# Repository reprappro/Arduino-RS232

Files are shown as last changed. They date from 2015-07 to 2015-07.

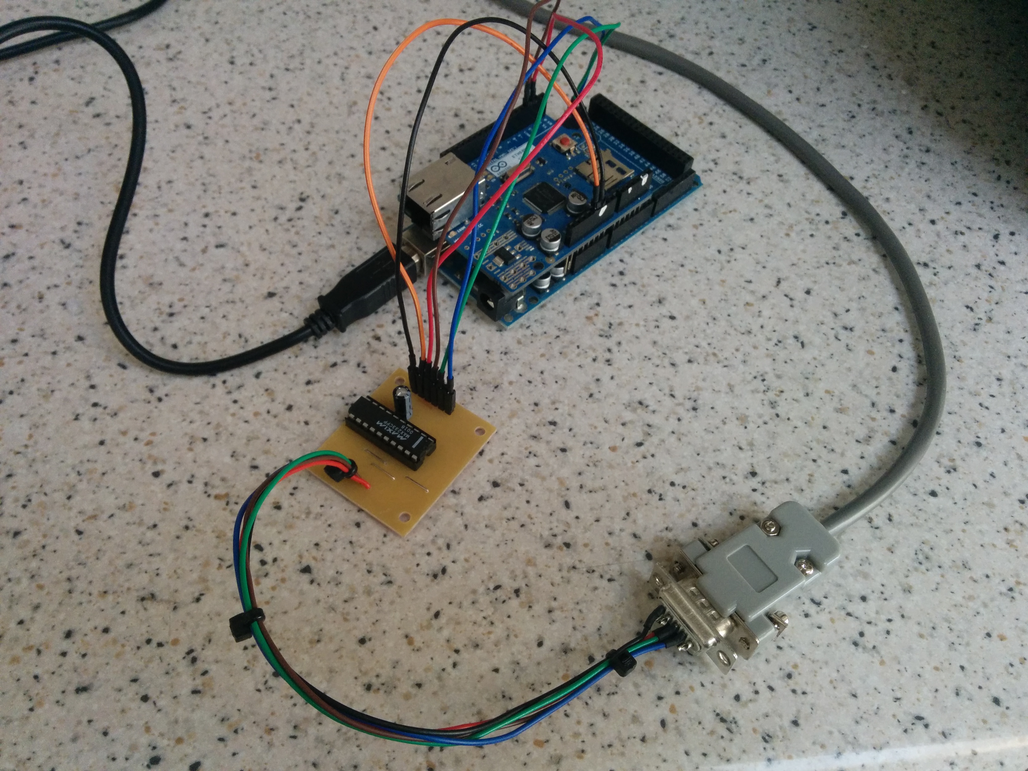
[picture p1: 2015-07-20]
Images/2015-07-17 16.40.09.jpg

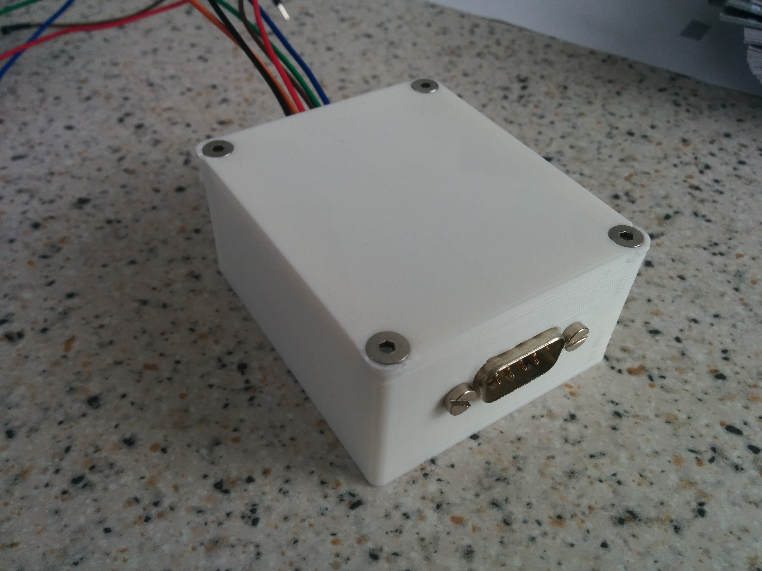
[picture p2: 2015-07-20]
Images/2015-07-20 14.40.57.jpg

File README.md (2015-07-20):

# Arduino-RS232
An RS232 interface circuit for Arduinos.  

It is general-purpose, but it is primarily intended to allow an Arduino to control
a Roland Modela CNC mill (http://www.rolanddg.com/product/3d/3d/mdx-20_15/spec.html).

This allows the Modela to mill PCBs under the control of the Arduino, including the PCB
for the interface circuit itself.  So you breadboard it and get it working.  Then you mill
its PCB.  Then you take the components off your breadboard and solder them onto the PCB...

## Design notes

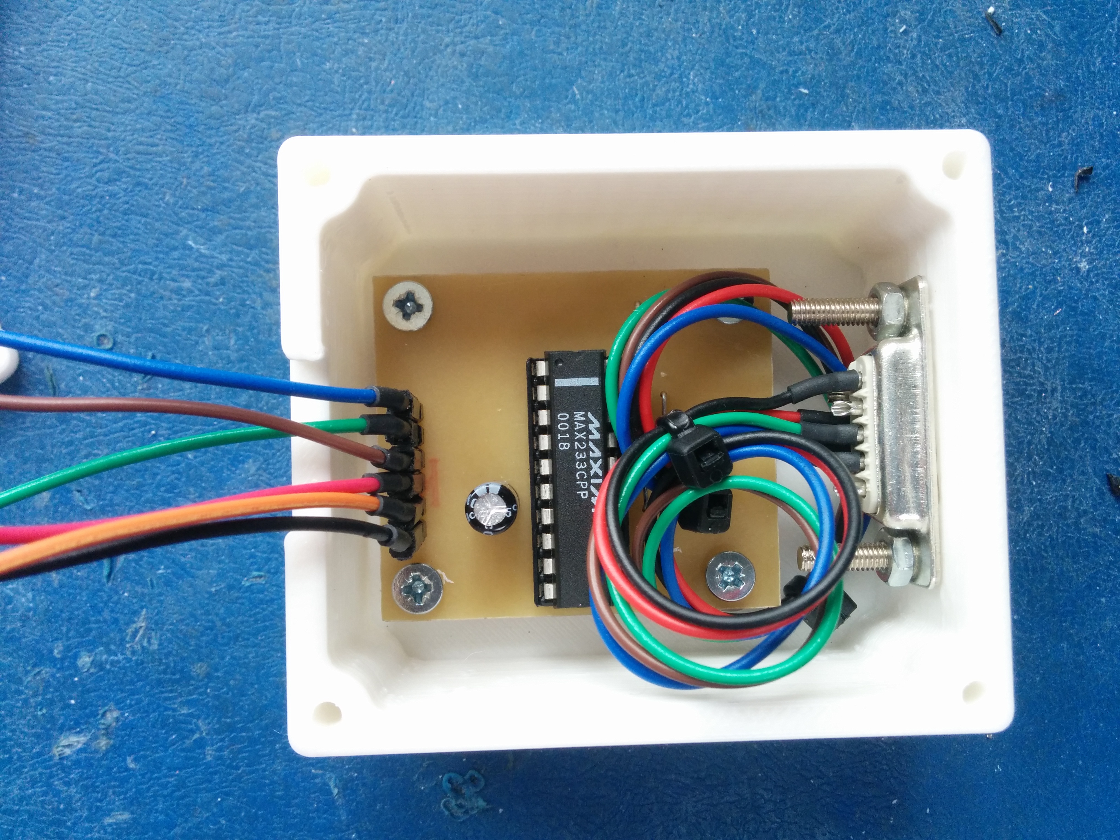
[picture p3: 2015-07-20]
Images/2015-07-20 13.38.10.jpg

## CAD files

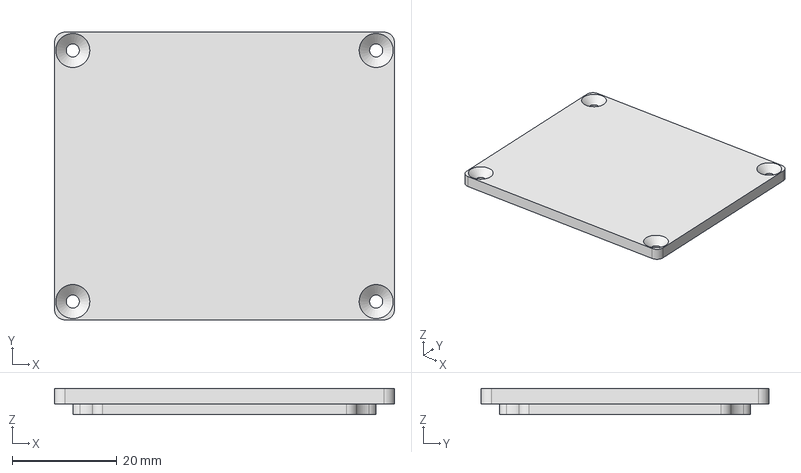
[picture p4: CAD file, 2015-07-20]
Case/Lid.stp
65.0 x 55.0 x 5.00 mm

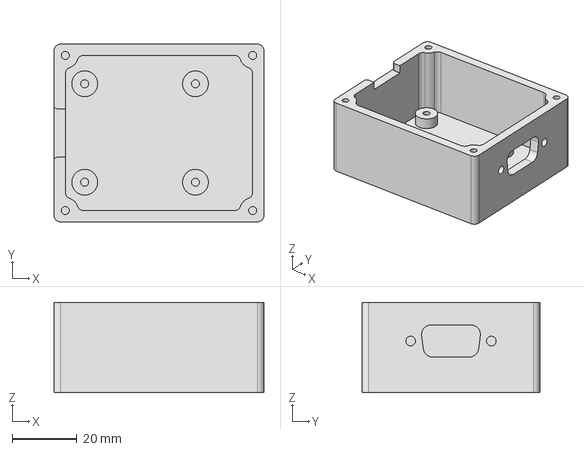
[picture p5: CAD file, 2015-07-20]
Case/Case.stp
65.0 x 55.0 x 28.0 mm

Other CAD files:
Case/Case.stl
Case/Lid.stl

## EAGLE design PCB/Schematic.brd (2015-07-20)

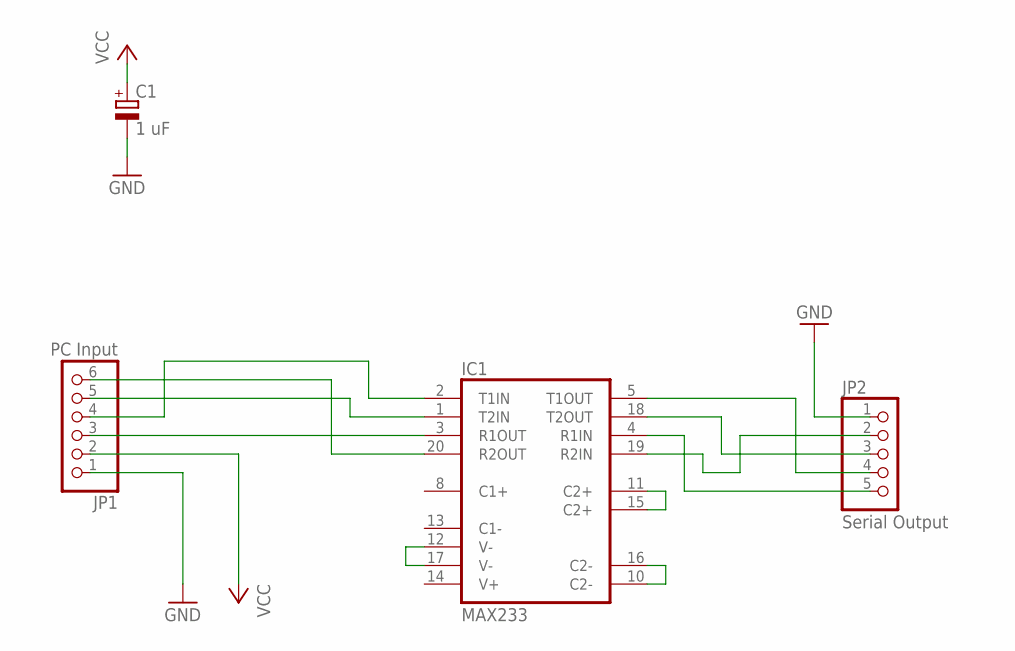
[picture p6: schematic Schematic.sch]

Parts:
C1: 1 uF; E2,5-6
IC1: MAX233; DIL20
JP1: PC Input; 1X06
JP2: Serial Output; 1X05

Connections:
GND: C1.-, IC1.6 (GND), IC1.9 (GND), JP1.1, JP2.1
unnamed: IC1.12 (V-), IC1.17 (V-)
unnamed: IC1.11 (C2+), IC1.15 (C2+)
unnamed: IC1.10 (C2-), IC1.16 (C2-)
unnamed: IC1.20 (R2OUT), JP1.6
unnamed: IC1.1 (T2IN), JP1.5
unnamed: IC1.2 (T1IN), JP1.4
unnamed: IC1.3 (R1OUT), JP1.3
unnamed: IC1.18 (T2OUT), JP2.3
unnamed: IC1.19 (R2IN), JP2.2
unnamed: IC1.5 (T1OUT), JP2.4
unnamed: IC1.4 (R1IN), JP2.5
VCC: C1.+, IC1.7 (VCC), JP1.2

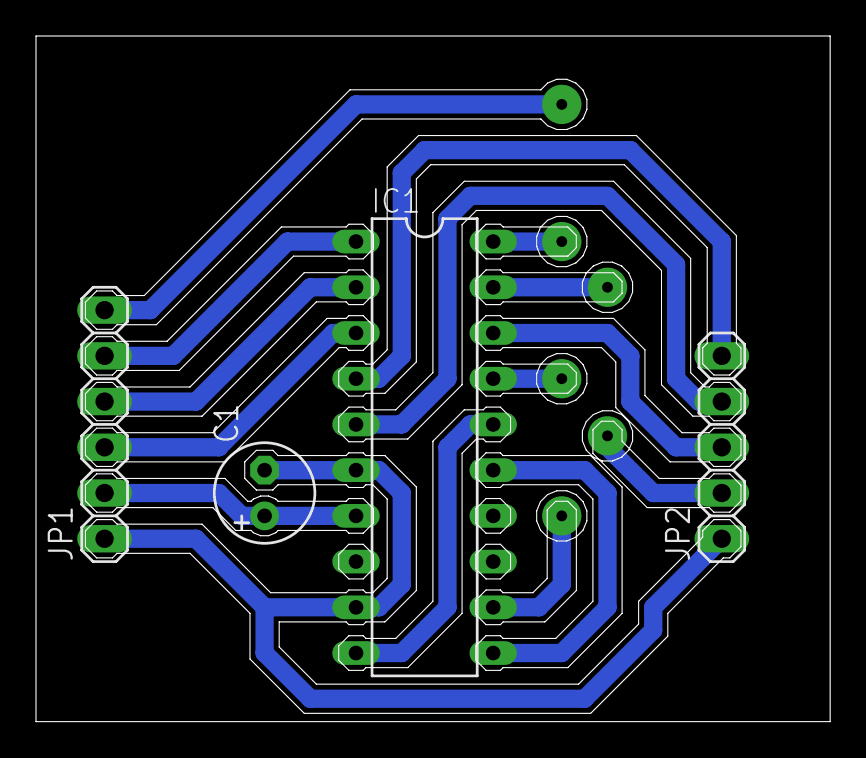
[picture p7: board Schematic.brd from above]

Board: 2 copper layers, 44.1 x 38.1 mm, 4 parts (0 on the bottom side), 13 nets.

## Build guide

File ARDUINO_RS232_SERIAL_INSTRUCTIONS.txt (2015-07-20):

Details about the RS232 driver circuit
--Written 20-07-2015 by Oliver Kesterton

The circuit was designed to allow an Arduino to control a Roland MDX-20 Modela CNC mill.

The circuit contains a MAX233 driver IC, and breaks out the TX, RX, RTS and CTS lines, enabling hardware flow control.

Header connections: Board layout:

	 _______________________________________________
	|						|
A	|						|
r	|						|	     
d	|  RX                          	    	GND     |	Serial
u	|  TX            			RX	|	Connector
i	|  RTS				   	TX	|
n	|  CTS			           	RTS	|
o	|  +5V				   	CTS	|
	|  GND						|
	|						|
	|_______________________________________________|

The system has been tested with an Arduino Mega with SD shield. It may work with other Arduino boards, but they will require at least
two serial ports. The MAX233 with 3.3V logic is untested.   

The Arduino program will make RTS (ready to send) high constantly, and will only send serial data when CTS (clear to send) is high.
Data is read from the SD card. Currently it looks for a file named "file.txt", but it should be relatively simple to modify the program
to ask for a filename, enabling any file to be read and sent.

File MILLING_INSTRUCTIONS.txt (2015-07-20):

Instructions for PCB milling on the Roland MDX-20 Modela mill, using the custom serial driver board.
--Written 20-07-2015 by Oliver Kesterton

-------To mill PCB once machine instruction file produced:------------

1-Copy the milling file to the micro SD card, and rename it to "file.txt"
2-Plug everthing in (Arduino Mega pin mapping):
	Black = GND
	Orange = +5V
	Blue = RX = 19
	Green = TX = 18
	Red = CTS = 2
	Brown = RTS = 3

	If connections have come out of PCB, order is:
		Blue
		Green
		Brown
		Red
		Orange
		Black

3-Open serial monitor via Arduino software
4-Switch the mill on at the wall, and press the standby button. The power LED should light up
5-Press the 'View' button. The mill should move to the bottom left position (0,0 xy position). The tool z position will not change.
6a-Press 'Down' for a short time, so that the tool moves down a bit, but is still well above the work surface
	RUN THE CODE FOR THE FIRST TIME IN THIS STATE, IN ORDER TO CHECK IT IS DOING WHAT IT SHOULD. ONCE SATISFIED IT IS
	RETURN TO INSTRUCTION 6b.

6b-Press 'Down' until the tool is just above the PCB, then adjust the tool until it is just touching the work surface.
	(unscrew the grub screw and let it drop out)
	-For files produced using the eagle add on, with no changes made to the file, the z tool-height is set wrong.
	Instead, lower the tool into the PCB slightly, to the desired cutting depth (about 3 presses of 'Down' is usually plenty).
	Note that the tool will move up before its first cut.
7-The Arduino serial monitor should say "Type G to begin". If not, press the reset button.
	Type 'G' (note, it is case sensitive) in the serial monitor and click send. The machine should begin cutting.
	Watch the tool closely initially. If it is doing weird things, press 'View' to pause the cut.
	Pressing 'View' again will return the tool to where it was
8-Once complete, the tool will return to the 0,0 position. Press 'View' to return the tool to its resting position, and extract the board.

To cancel a print, press 'View'. Once the tool has moved to its idle position, press the reset button on the Arduino and press the 
	'Up' and 'Down' buttons together to delete remaining commands from the buffer. The view LED will flash whilst this happens
	and will stop flashing once the program has been deleted.

--------------------------------------------------------------------------------------

--To generate milling script (RML-1 files)--------------------------------------------

Option 1 (easiest): CopperCAM (http://www.galaad.net/coppercam-eng.html)
	The program will open Gerber files and output RML-1 script.
	The program is fairly intutitive with good documentation. The generated RML-1 files work straight from the program.
	However, the program requires an 80 Euro licence.

Option 2: Eagle and a script to output RML-1 file (Detailed instructions here: http://mlab.taik.fi/paja/?p=1874)
	-In your Eagle install, change replace the eagle.def file with the one included in the "Eagle scripts" folder
	-In Eagle, go File>Run ULP and naviagate to fablab-mill-n-drill.ulp. 
		This should make some milling paths on layers 45 and 46 in Eagle
	-In the Eagle CAM processor, load the job fablab-mill-n-drill.CAM
		In each tab, change the X offset to be the width of the board, or greater. A Y offset is optional.
	-Click Process Job, and the RML-1 files should appear in the project directory.

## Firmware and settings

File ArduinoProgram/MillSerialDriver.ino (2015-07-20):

#include <SPI.h>
#include <SD.h>


char fileName[] = "file.txt";
char data;

int chipSelect = 4;
int RTS = 3;
int CTS = 2;

void setup() {
	pinMode(RTS,OUTPUT);
	pinMode(CTS,INPUT);
	
	digitalWrite(RTS,LOW); //Keep ready to send high, so mill knows data is available
	
  // Open serial communications and wait for port to open:
	Serial.begin(9600);//For usb comms
	Serial1.begin(9600);//For serial comms to mill
	
	Serial.println("Type G to begin");
	
}

void loop() {
	if (Serial.available() > 0){//Read serial data if available
		data = Serial.read();
		
		if (data == 'G'){
			Serial.println("Print started");
			
			if(SD.begin(chipSelect) == 0){
				Serial.println("SD INITIALIZATION ERROR");
				return;
			}else{
				Serial.println("Card initialised successfully");
				
				//Open file from SD card
				File sdFile = SD.open(fileName);
		
				if(sdFile == 1){
					Serial.print(fileName);
					Serial.println(" opened successfully. Beginning print");
		
					while(sdFile.available()>0){//file.available() returns number of bytes available				
					//Write file to serial if clear to send, and file not finished
						if (digitalRead(CTS) == 0){
							Serial1.write(sdFile.read());
						}
						//delay(100);
					}
					Serial.println("Print complete");
					sdFile.close(); //Close file when finished
				}else{
					Serial.println("ERROR, file not found");
				}
			}	
		}
	}	
}

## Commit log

2015-07-20 All files for RS232 Driver Added
    [Case.stl, Lid.stl, Schematic.brd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]
2015-07-20 STEP Files for case added
    [Case.stp, Lid.stp]
